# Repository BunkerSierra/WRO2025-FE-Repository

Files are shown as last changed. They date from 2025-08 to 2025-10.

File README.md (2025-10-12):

# Team Bunker Sierra – WRO Future Engineers 2025

We are a team from Baja California, México, composed of two members: Diego Alejandro Salas Díaz and Jacobo Arteaga Castañeda from Bunker Robotics. Both team members have experience in other competitions, specifically the Robomission category, totaling 8 years of combined experience.

This is our first year in the Future Engineers category. We began our preparation at the start of the year (January 2025), and over time, our robot has gone through several iterations. In fact, our current robot looks significantly different from the version used in the regional stage.

The following photo shows the 3 team members (from left to right):

Jacobo Arteaga Castañeda - Diego Alejandro Salas Díaz - Andrea Perez Bueno (Coach)

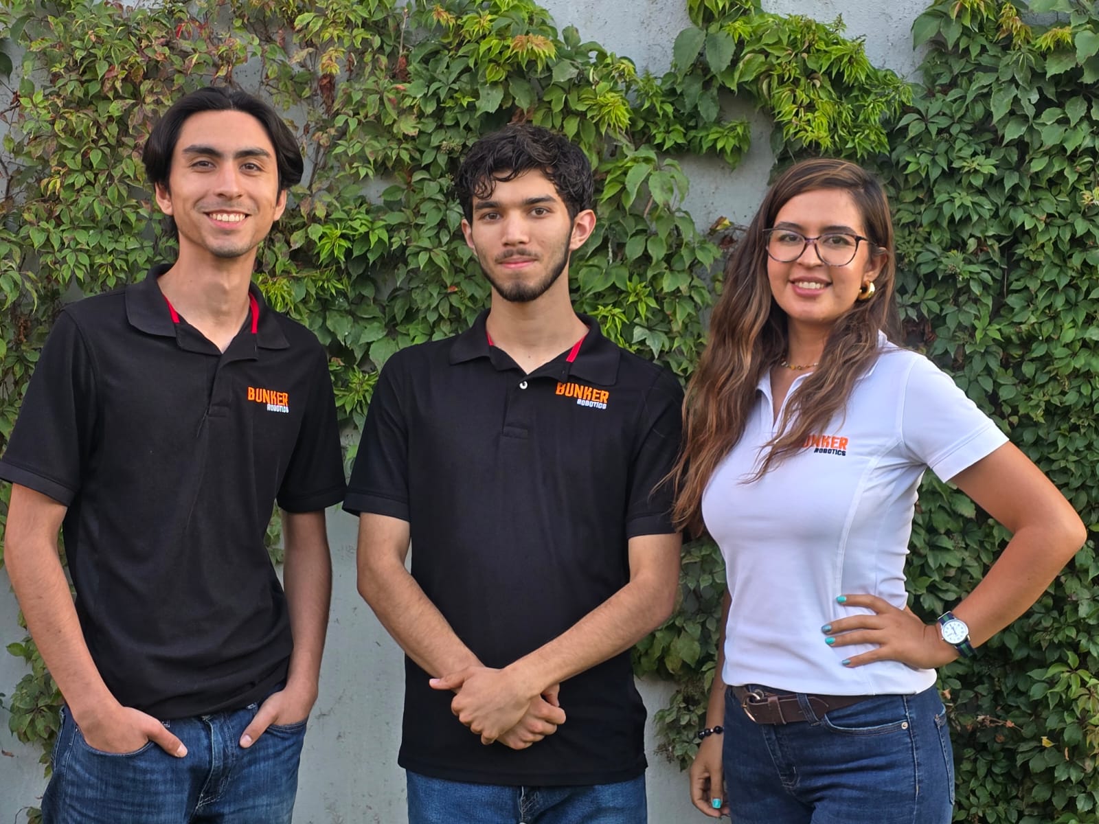
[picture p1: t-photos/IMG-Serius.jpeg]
IMG-Serius


In this document, we will detail our robot's components, their functions, and how they work together. We will also explain some of the key changes we have made to the robot, supported by visual evidence.

Please note: All requested supplementary information will be available in its corresponding folder within the repository.

## Robot Specifications:

**Vehicle photos rev.14 (Mexico National Final):**
| View | Photo |
|---|---|
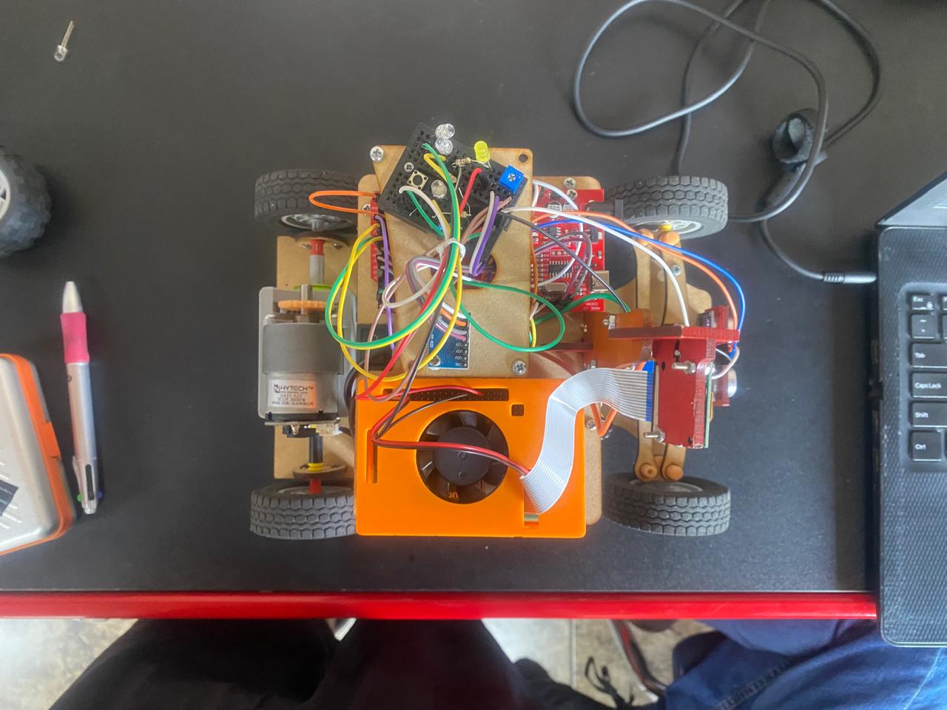
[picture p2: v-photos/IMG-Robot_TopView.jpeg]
IMG-Robot_TopView
| Top View |  |
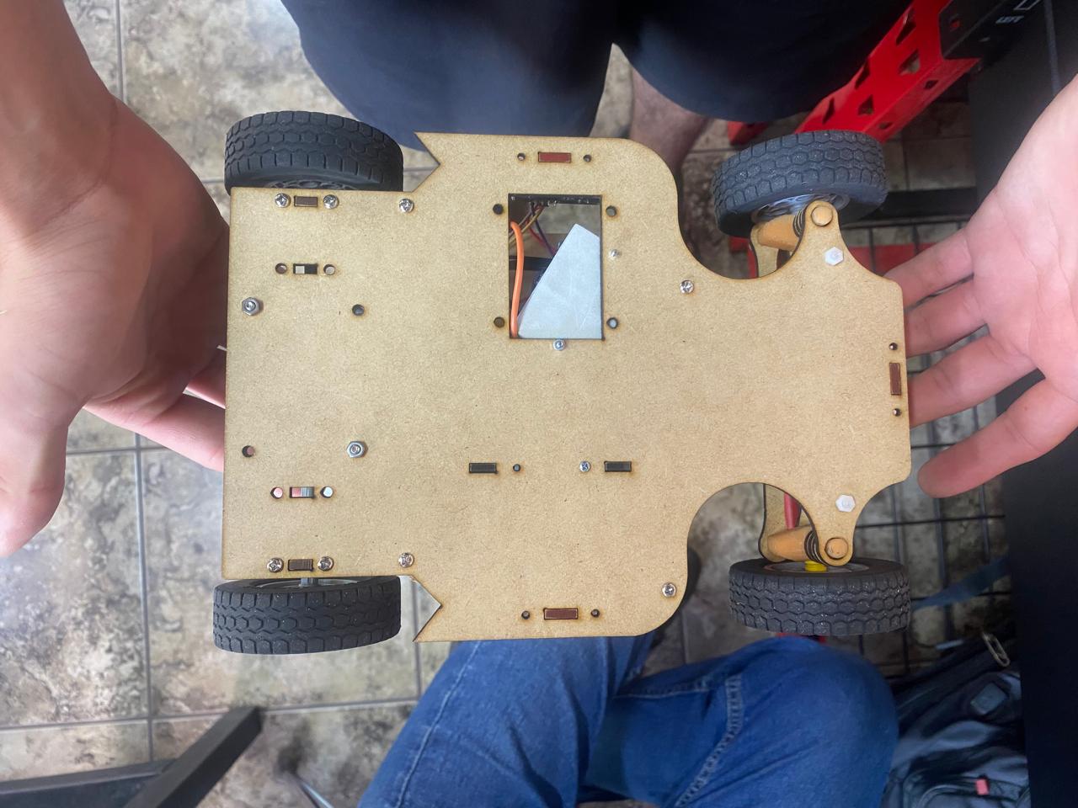
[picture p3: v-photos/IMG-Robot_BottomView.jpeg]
IMG-Robot_BottomView
| Bottom View |  |
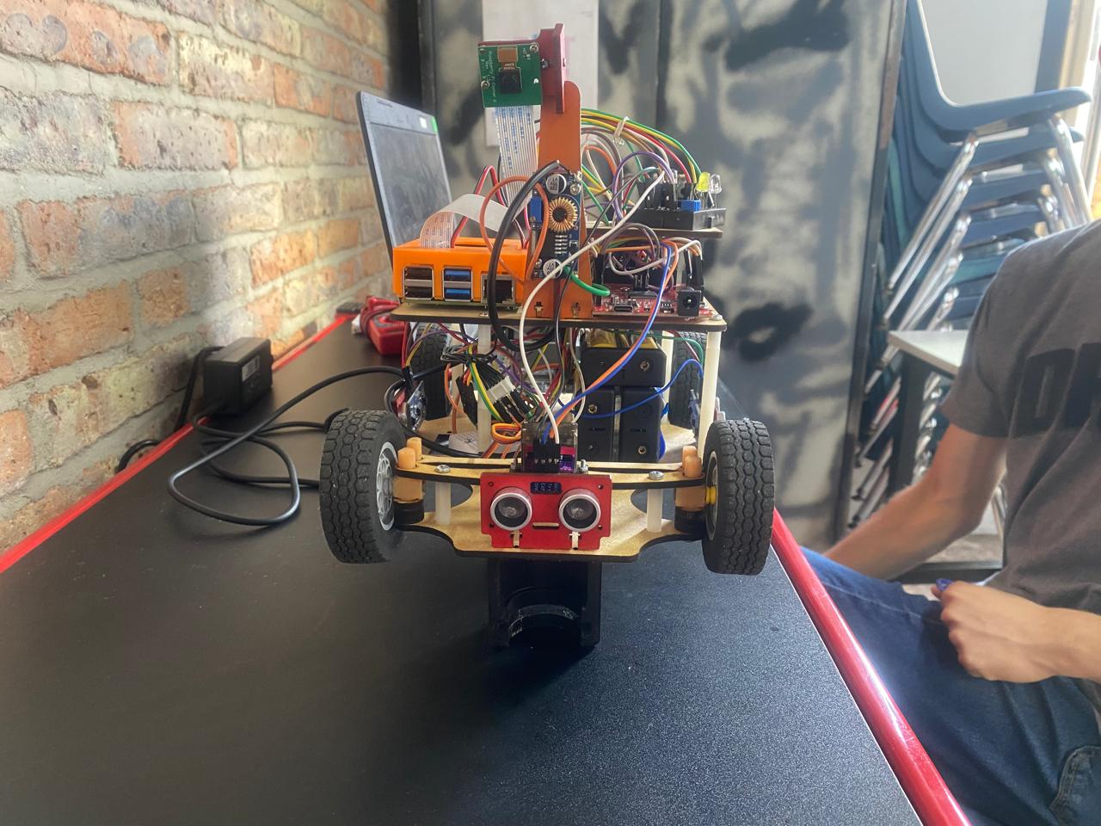
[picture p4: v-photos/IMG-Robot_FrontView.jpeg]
IMG-Robot_FrontView
| Front View |  |
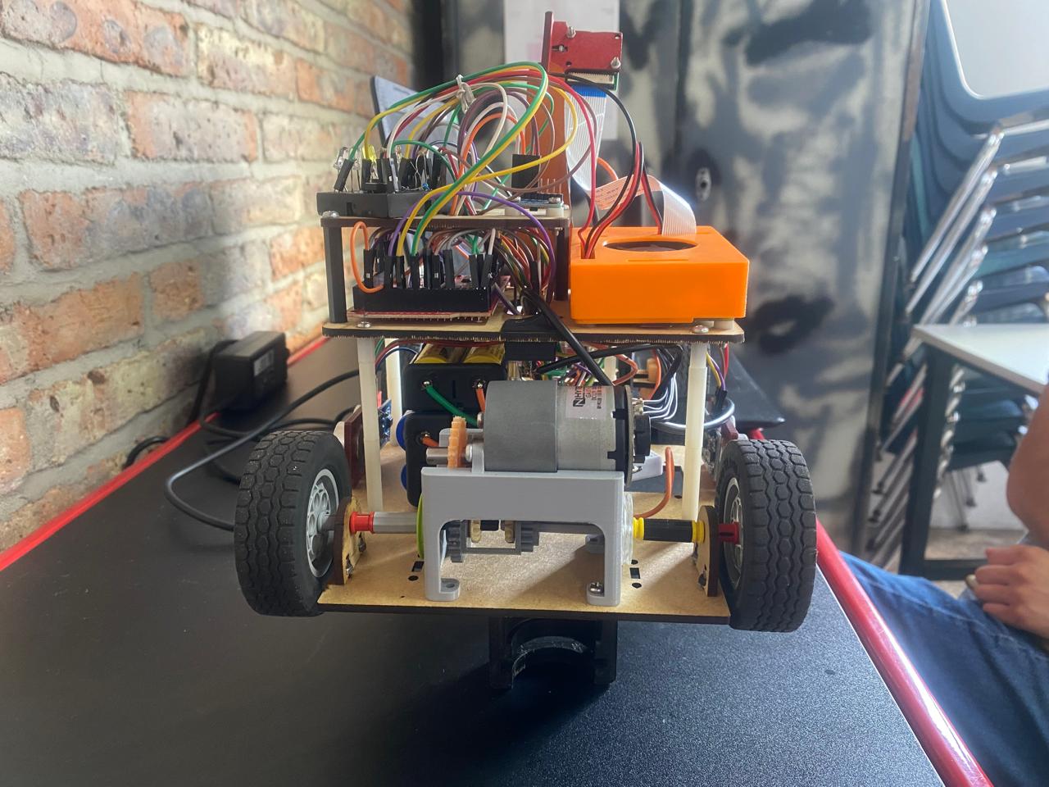
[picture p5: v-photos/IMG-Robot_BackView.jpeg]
IMG-Robot_BackView
| Back View |  |
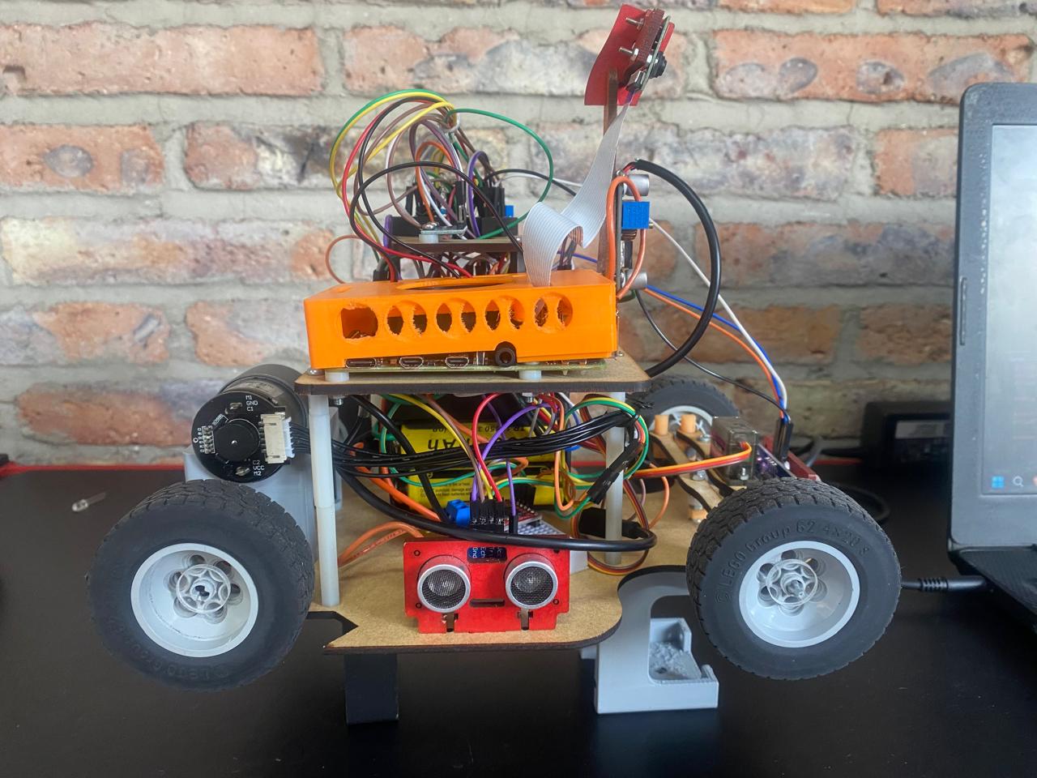
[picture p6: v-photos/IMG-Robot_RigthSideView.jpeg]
IMG-Robot_RigthSideView
| Right View |  |
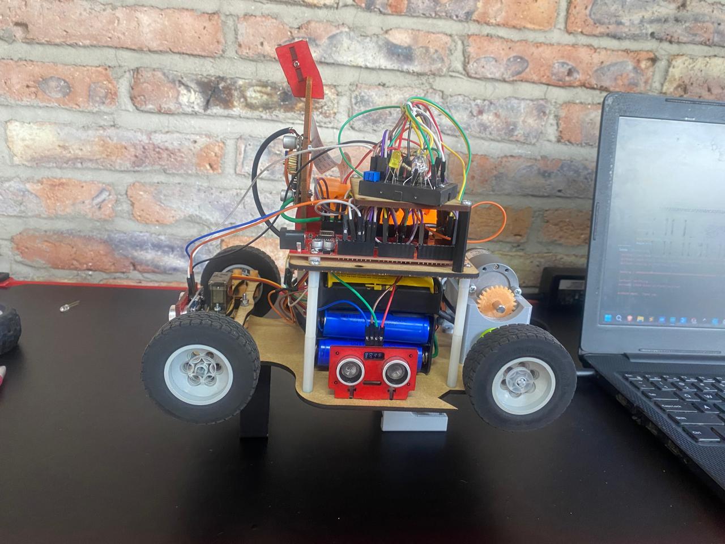
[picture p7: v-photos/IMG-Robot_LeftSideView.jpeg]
IMG-Robot_LeftSideView.
| Left View |  |

**Vehicle photos rev.15 (New rev. for OC Panama):**
| View | Photo |
|---|---|
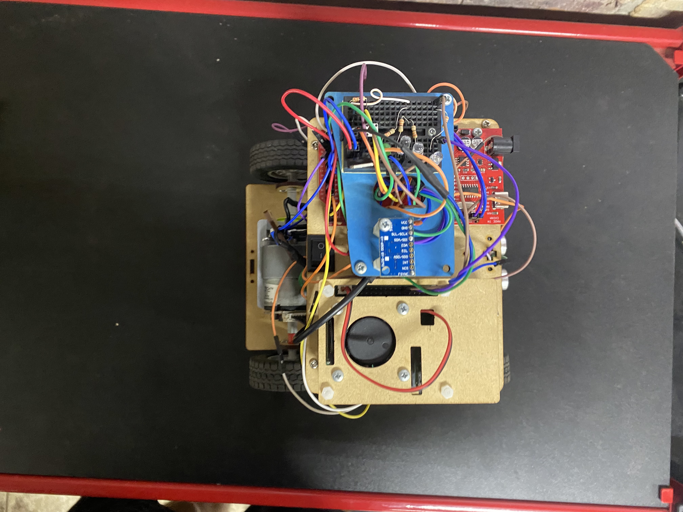
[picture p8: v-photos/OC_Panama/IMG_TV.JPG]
IMG_TV
| Top View |  |
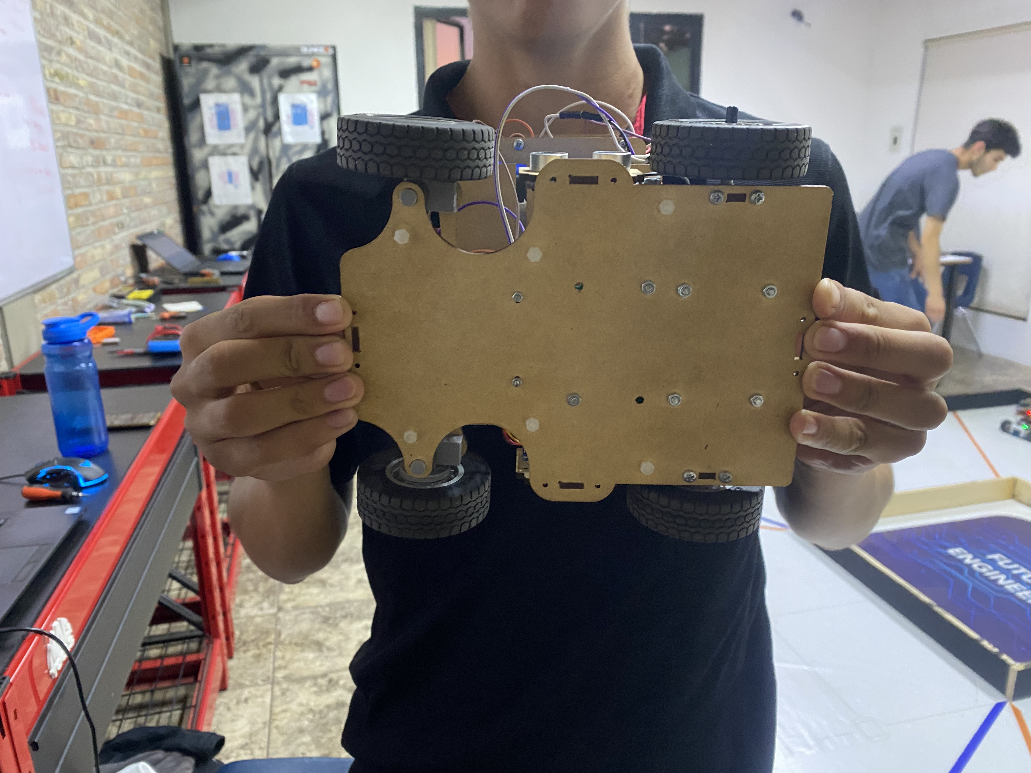
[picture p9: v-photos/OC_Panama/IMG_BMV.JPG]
IMG_BMV
| Bottom View |  |
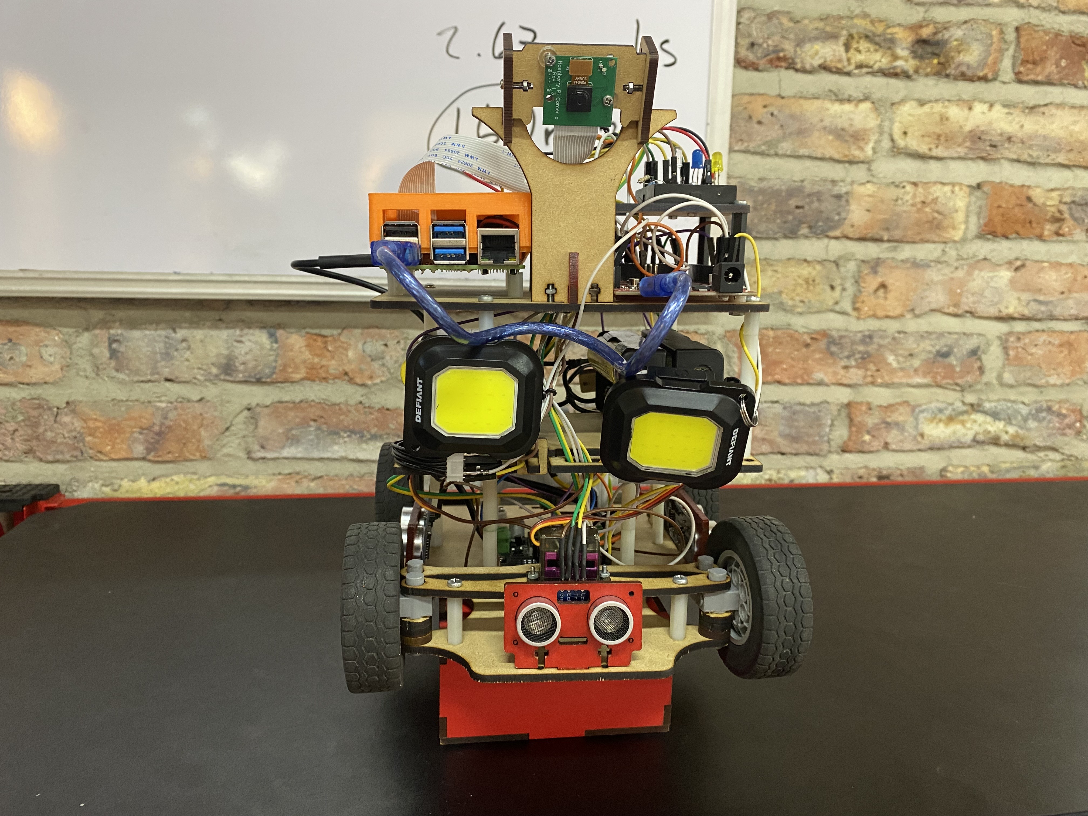
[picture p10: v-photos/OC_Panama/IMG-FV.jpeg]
IMG_FV
| Front View |  |
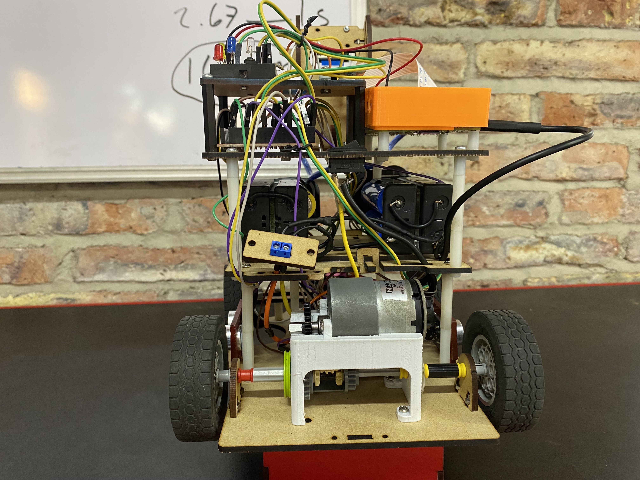
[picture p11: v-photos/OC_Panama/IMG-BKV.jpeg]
IMG_BKV
| Back View |  |
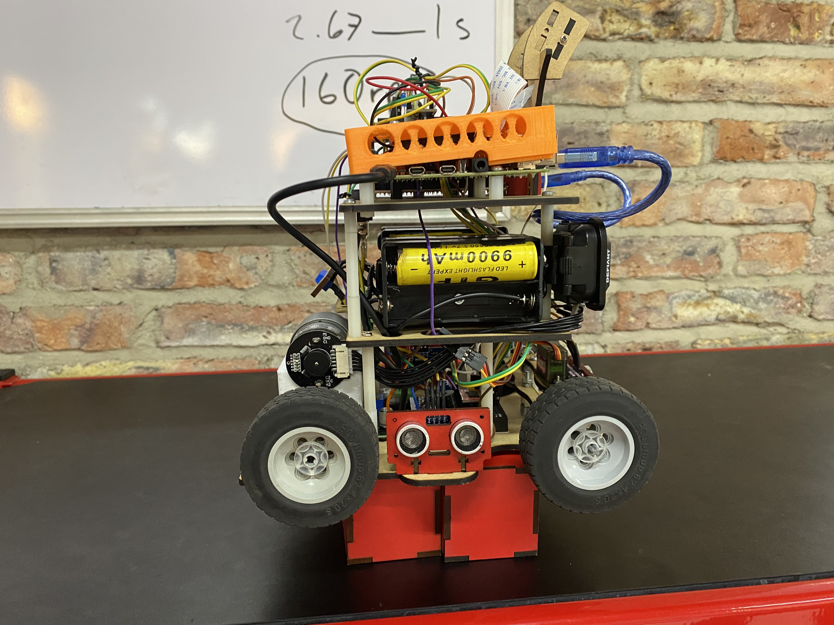
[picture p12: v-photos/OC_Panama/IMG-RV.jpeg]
IMG_RV
| Right View |  |
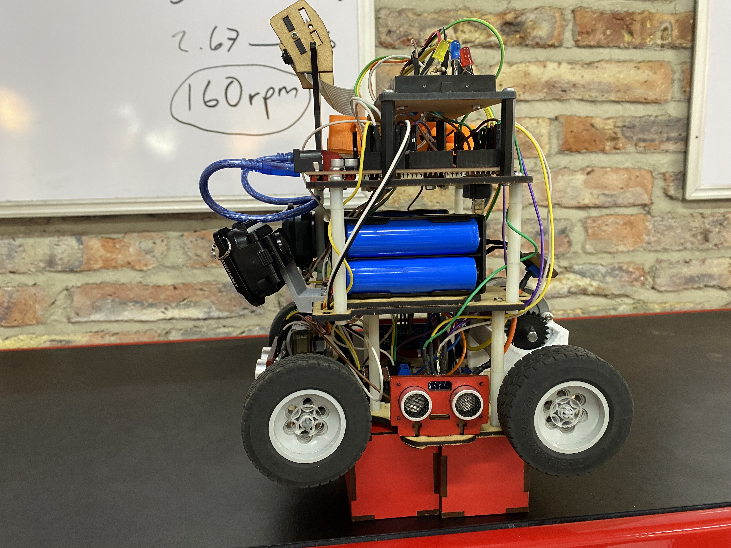
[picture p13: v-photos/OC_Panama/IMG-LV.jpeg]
IMG_LV
| Left View |  |

- **Weight (Maximum Load):** 1166 grams.
- **Width:** 1.5cm | **Length** 19.5cm | **Heigth:** 23.9cm

**Robot Bill of Materials (BOM)**

| Component | Power Requirements | Image | Price |
|---|---|---|---|
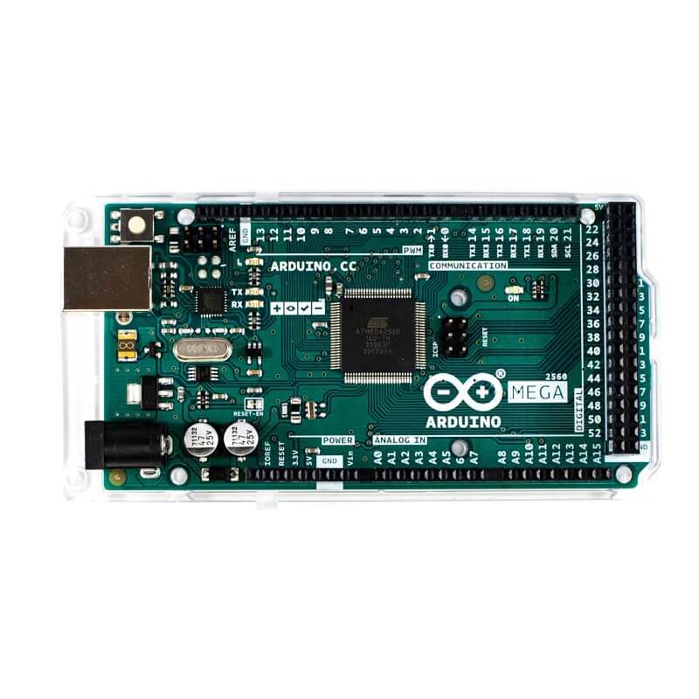
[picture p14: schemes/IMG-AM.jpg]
IMG-AM
| Arduino Mega 2560 | 0.25-0.5W |  | ≈ 24.46 Dlls |
| Raspberry Pi 4 Model B (1GB RAM) | 3.06-6.12W | IMG-RBPi4 | ≈ 46.90 Dlls |
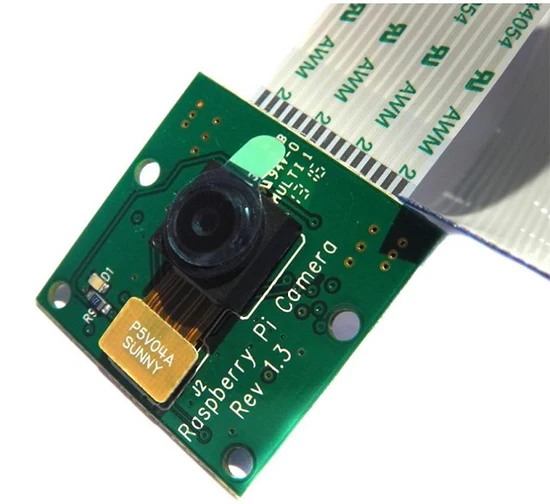
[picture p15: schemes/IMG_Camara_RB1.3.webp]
IMG_Camara_RB1.3
| Raspberry Pi Camera Rev 1.3 | 0.83W |  | ≈ 25 Dlls |
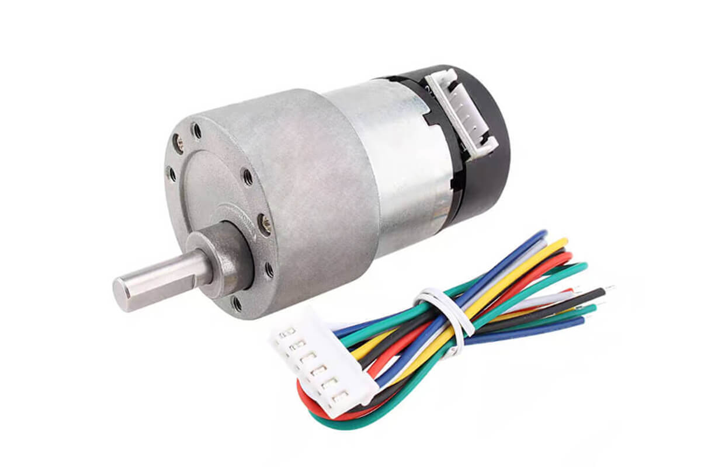
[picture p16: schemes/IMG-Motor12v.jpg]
IMG-Motor12v
| DC Motor with Encoder: GA37-520 300RPM | 5.55-16.65W |  | ≈ 22.12 Dlls |
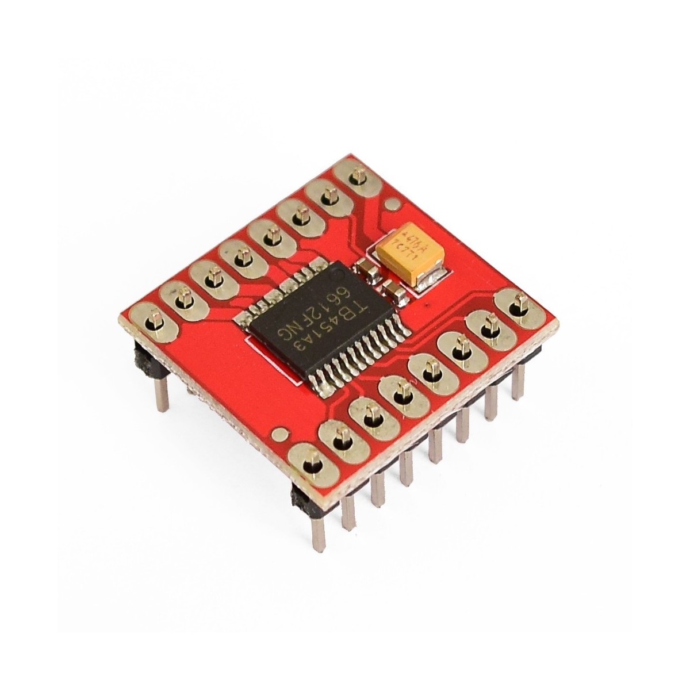
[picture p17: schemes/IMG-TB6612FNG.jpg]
IMG-TB6612FNG
| H-Bridge TB6612FNG | 0.025W |  | ≈ 4.35 Dlls |
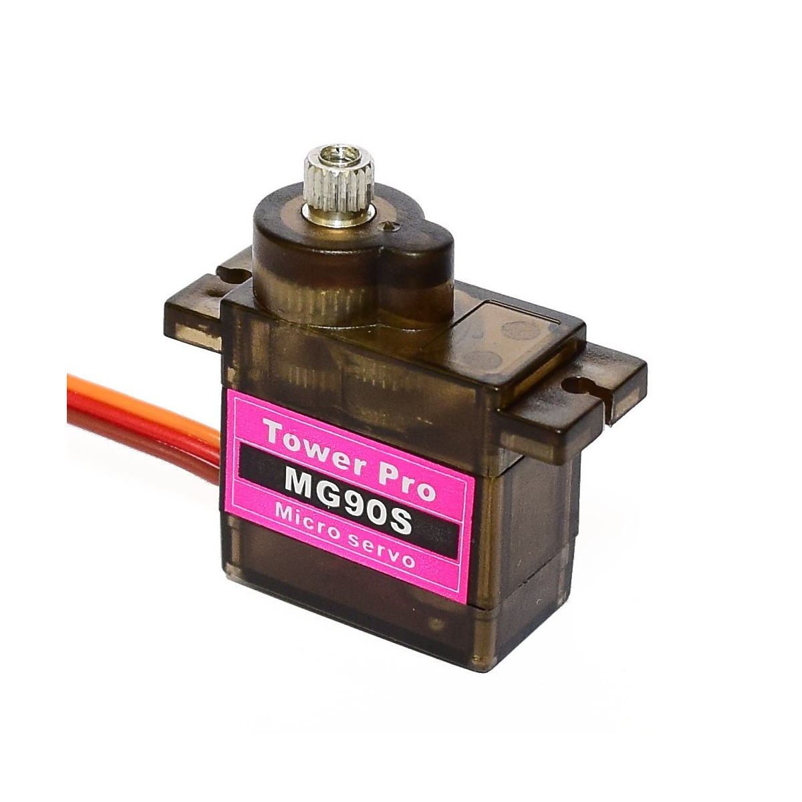
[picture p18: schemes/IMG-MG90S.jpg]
IMG-MG90S
| Servo Motor: MG90S | 0.5-2.5W |  | ≈ 4.08 Dlls |
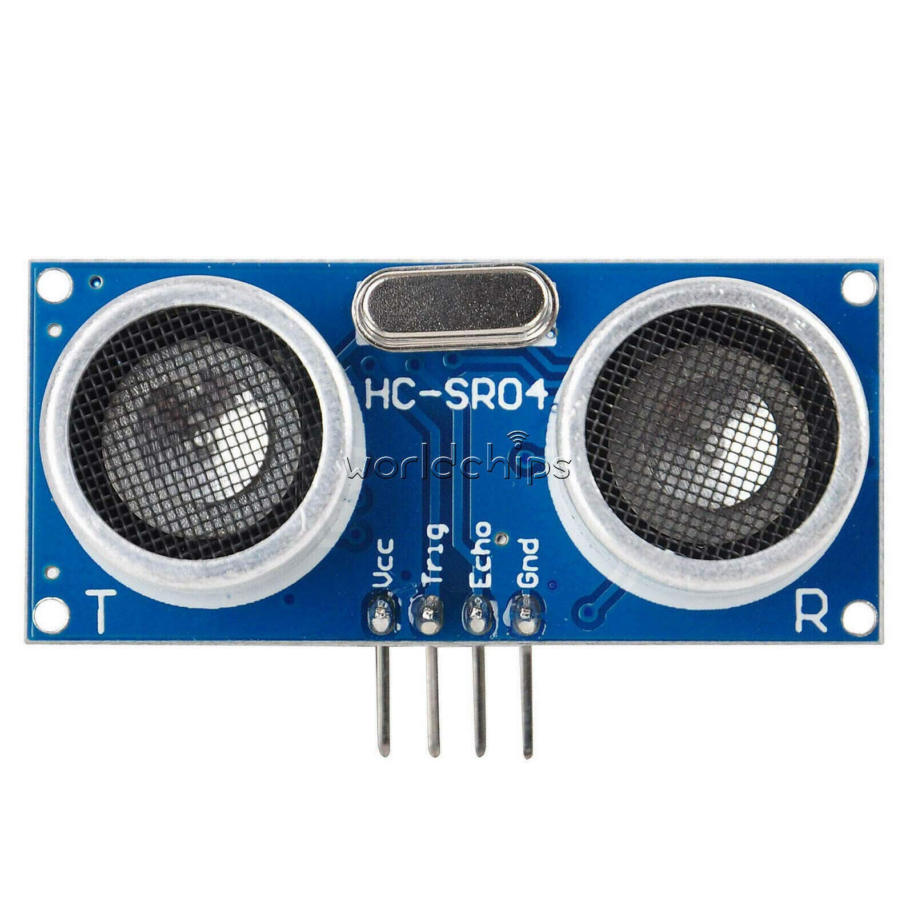
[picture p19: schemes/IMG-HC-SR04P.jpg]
IMG-HC-SR04P
| Ultrasonic Sensors: HC-SR04P x3 | 0.225W |  | ≈ 2.72 Dlls **(one unit)** |
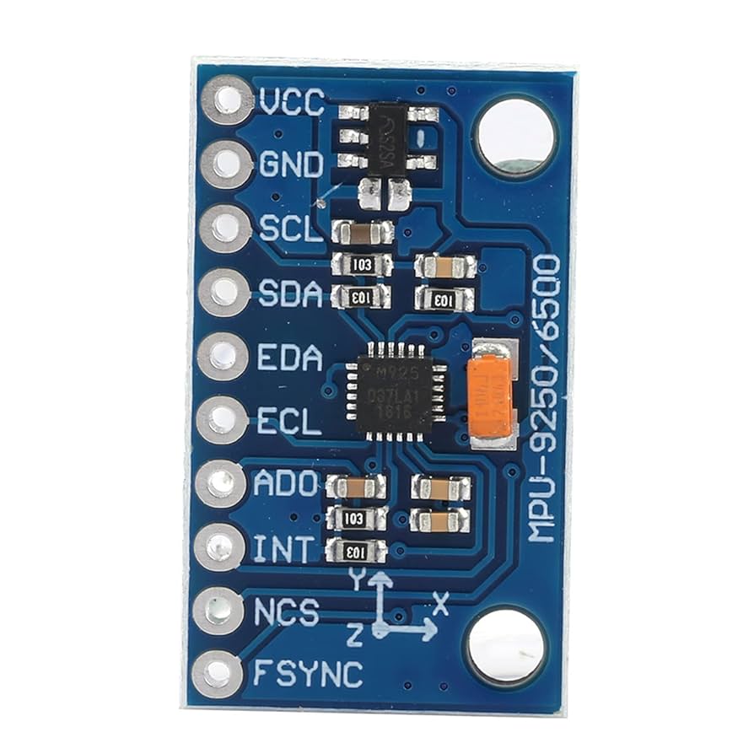
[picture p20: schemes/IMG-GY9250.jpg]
IMG-GY9250
| Accelerometer/Gyroscope: GY-9250 | 0.033W |  | ≈ 9.24 Dlls |
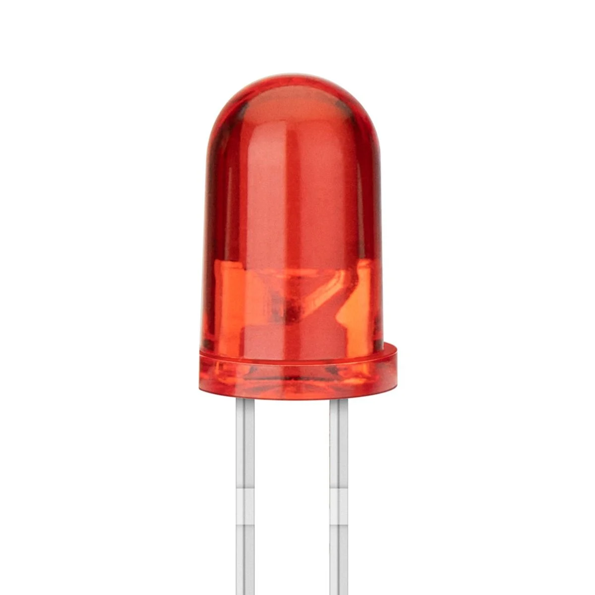
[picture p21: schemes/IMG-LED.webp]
IMG-LED
| LEDs x4 | 0.264W |  | ≈ 0.11 Dlls **(one unit)** |
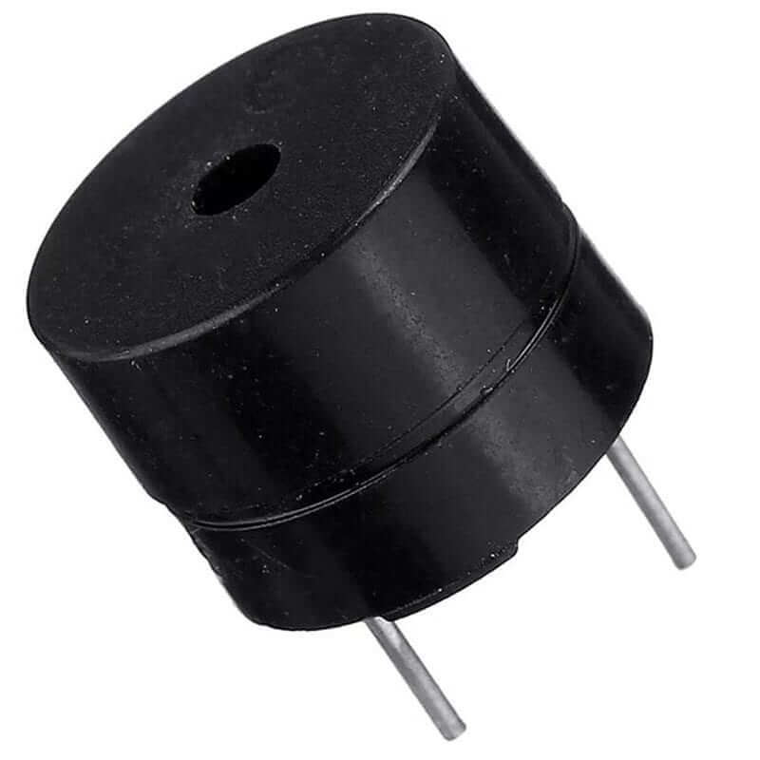
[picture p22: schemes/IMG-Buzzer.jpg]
| Passive Buzzer |  |  | ≈ 0.27 Dlls |
| **Total** | --- | --- | **≈ 145.02 Dlls** |

*Electrical Parts:*

- Arduino Mega 2560

- Raspberry Pi 4 Model B (1GB RAM)

- Raspberry Pi Camera Rev 1.3

- Motor Driver: IMS-2 WINGXINE

  - **Update 20/08/2025:** H-Bridge TB6612FNG

- Voltage Regulator: LM2596 Step-Down Module

- DC Motor with Encoder: GA37-520 300RPM

- Servo Motor: MG90S

- 3x Ultrasonic Sensors: HC-SR04P

- Accelerometer/Gyroscope: MPU-6050

  - **Update 12/09/2025:** Accelerometer/Gyroscope: GY-9250

- 4x LEDs

- Batteries: 6x 3.7v 18650 9900mAh

  - **Update 14/09/2025:** 8x 3.7v 18650 9900mAh

  - **Update 25/09/2025:** 3x 3.7v 18650 3000mAh
    
  - **Update 02/10/2025:** 6x 3.7v 18650 3000mAh

- Battery Holders: 3x 18650 Holders

  - **Update 14/09/2025:** 4x 18650 Holders

  - **Update 25/09/2025:** 2x 18650 Holders
    
  - **Update 02/10/2025:** 4x 18650 Holders

- 1x Passive Buzzer

- 2x Mini Protoboards

*Mechanical Parts:*

- MDF Chassis x3

- MDF Linkage Steering System

- 4x Lego Wheels (62.4mm x 20mm)

- 3D-Printed Motor Mount

- Raspberry Pi Camera Rev 1.3 Mounts

- 3x Ultrasonic Sensor Mounts

- Lego Differential Gear

- 3D-Printed Spur Gear (24-tooth)

- Lego Technic Parts

**Update 25/09/2025**

***Update for the Panama Open Championship***

We have implemented several changes to the robot's design, specifically focusing on reducing its footprint. In other words, we have reduced the robot's width and length while taking full advantage of the established height limit (30 cm). We have redistributed the components accordingly to optimize the use of space.

Here is the list of the STL desings of all the parts of the robot chassis that where changed:

- [S25 Chassis Rev15B](/models/Open_Championship_Panama/S25_Chasis_Rev15B.STL).
- [BS Batteries Rev3.STL](/models/Open_Championship_Panama/BS_Baterias_Rev3.STL).
- [C3 Batteries Rev3.STL](/models/Open_Championship_Panama/C3_Baterias_Rev3.STL).
- [S25 Level 3 Rev3.STL](/models/Open_Championship_Panama/S25_3er_Piso_Rev3.STL).

We have also significantly reduced the robot's turning circumference. Previously, when the robot executed a full turn, the diameter of the circle it traced was 62 cm. This was quite large and allowed the robot to collide easily with the field's barriers and obstacles (in both challenges). By reducing the robot's overall size, the turning circle diameter is now 30 cm. We managed to cut it in half, giving the robot a greater margin of error to avoid collisions with various objects on the field. 

Another major change was made to the robot's power system. To be frank, our previous design was poorly planned. For the Open Championship, we opted to use **two packs in parallel of three 3.7V 30000mAh batteries connected in series(3S2P)**. 

Finally, we added two lamps to the robot to improve our camera's optics. By generating our own light source, detecting obstacles becomes a simpler task, as it no longer depends on the varying light conditions and parameters of the different environments where the robot operates. 

Here is the list of the STL desings of the camera parts that where changed:

- [Light L Mount](/models/Open_Championship_Panama/Soporte_L_Rev1.STL).
- [Camera Mount_Rev3](/models/Open_Championship_Panama/Soporte_Camara_Rev3.STL).

This is the brand and especifc model of the lamps tha wew used: **Defiant 226 129**

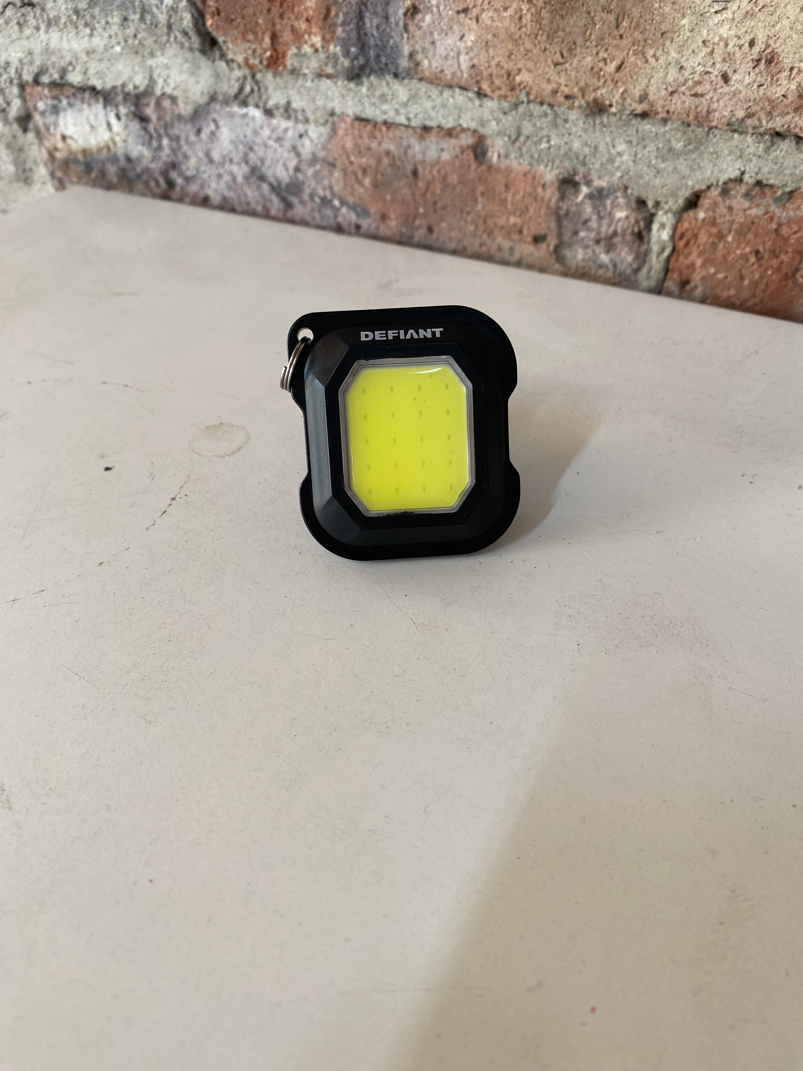
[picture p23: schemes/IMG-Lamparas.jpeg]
IMG-Lamparas


Mechanical Parts
===

*You are about to see all the information contained in our [models](/models/README.md). folder. If you wish to only view the information from this specific section, you can access it directly via the hyperlink (with the exception of the updates for the Panama Open Championship).*

One key point we would like to emphasize is that the majority of our mechanical parts were manufactured using laser cutting. Another small section of parts, primarily for the steering system, were 3D-printed.

## Vehicle Chasis
The vehicle consists of a chassis and two additional levels (floors), each housing different robot components:

- **Chassis:** Robot Motion Management
  - Steering system, DC drive motor, Motor driver, and a Mini Protoboard.
  - [Chassis View](/models/S25_Chasis_Rev12.STL).
- **Level 1:** Robot Controllers
  - Arduino Mega, Raspberry Pi y RaspBerry pi Camara rev 1.3
  - [Level 1 View](/models/S25_BS_Rev6.STL).
- **Level 2:** Electrical Components
  - Mini Protoboard with HMI and Gyro sensor.
  - [Level 2 View](/models/S25_Piso3_Rev1.STL).
 
As you may notice, the filenames for all models include their revision number. For example, the chassis is on its 12th revision. This reflects every change we have needed to make throughout the season. It is the part that has undergone the most changes.

As mentioned in other sections of the repository, our robot looked very different during the regional stage compared to its current form for the national stage. This is the main reason why this particular part has been modified so extensively. It was from **Rev8** onwards that it began to take on its current appearance.

**Update 14/09/2025**

**1. Chassis and Power System Modification**

**Motivation:** During performance testing for the obstacle challenge, we observed excessive energy consumption from the Raspberry Pi module. This was causing a rapid voltage drop in the batteries (~0.08V per complete run), which compromised the robot's operational autonomy to successfully complete multiple attempts or competition rounds.

**Implemented Solution:** To resolve this energy bottleneck, we expanded the power system by integrating a fourth battery holder, connected in parallel with the existing ones. This configuration:

**Increases the total capacity (Ah)** of the battery bank.

**Maintains the nominal operating voltage** for all components.

**Provides greater autonomy** by distributing the current demand across more power sources.

**Additional Changes:** As part of the chassis reconfiguration, we re-optimized the placement of the voltage regulator and the protoboard to improve accessibility, aesthetics, and cable management.

- [S25_Chasis_Rev14](/models/S25_Chasis_Rev14.STL).

To keep the battery holders securely in place, we designed another component (there are two of these in the robot) capable of holding two battery holders simultaneously. You can view the part here:

- [SB_DrakoR_Rev2](/models/SB_DrakoR_Rev2.STL).

## Mobility Management
**Motor Mount**

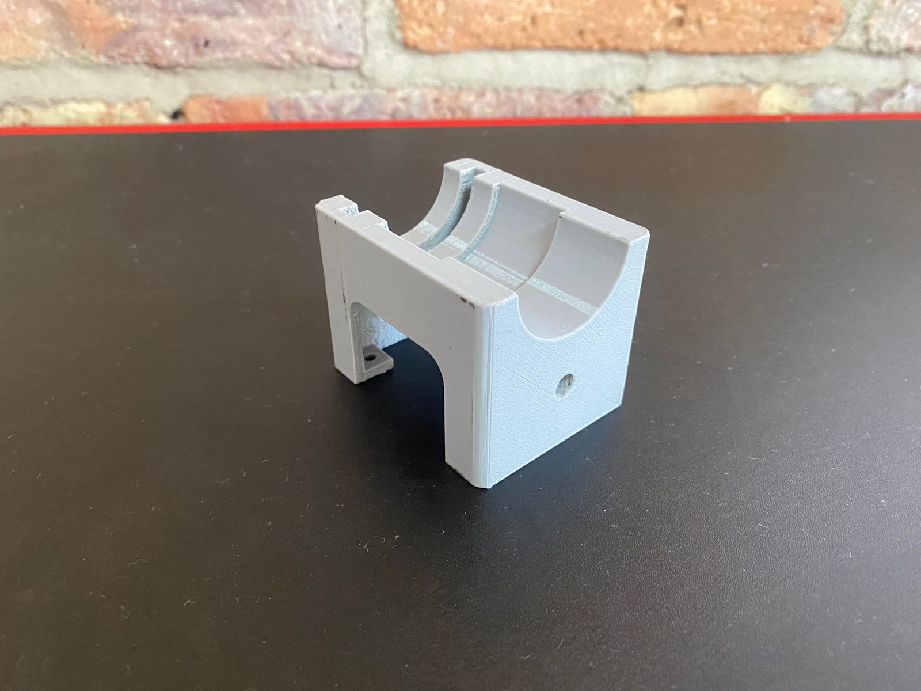
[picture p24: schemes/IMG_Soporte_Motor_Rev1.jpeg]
IMG_Soporte_Motor_Rev1


*This is what the first version looked like. It allowed for basic testing, but the motor was not secured to the mount, which caused disturbances and instability.*

-[Soporte para motor Rev3](/models/S25_Soporte_Motor_y_Transmision_Rev3.STL) 

*In the current revision, the motor is firmly secured to the mount, eliminating disturbances caused by movement.* We had a similar case with the gear that connects to the motor.

**Motor Axle Support**

The output shaft of our motor couples to LEGO axles that are connected directly to the wheels. During initial testing, we noticed that these axles were bending. This created an undesired additional force on the motor's Z-axis and caused inconsistent performance in each test run.

As a solution, we designed and implemented a custom support for these axles. Once installed, the axles remain perfectly aligned at a 180° angle, eliminating bending and ensuring uniform and predictable behavior.
- [Motor Axle support](/models/S25_Soporte_Eje_Motor_Rev1.STL).

**24-Tooth Spur Gear**

Initially, we used a standard 24-tooth LEGO Spur gear, drilling out its center to fit the motor's main shaft. This allowed us to validate the behavior of the differential system.

However, this provisional solution had two critical problems: the hole was quickly deformed by wear and tear, and it generated considerable backlash. To resolve this, we designed our own gear, maintaining the standard LEGO dimensions but with the exact inner diameter for our shaft. This ensured a perfect fit and eliminated the backlash.

- **Old Gear:**

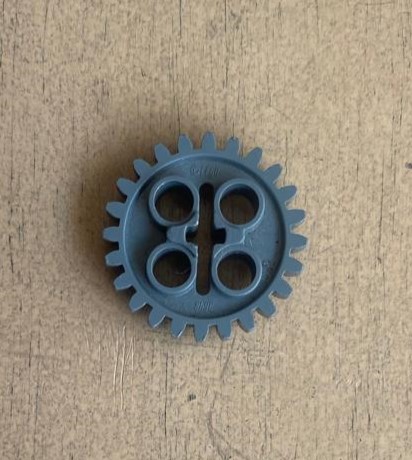
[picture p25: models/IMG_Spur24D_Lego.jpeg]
IMG_Spur24D_Lego
  - 

- **Proposed Gear by the Team:**

  - [New Custom Gear](/models/S25_Spur_24D_Rev3.STL)

**Steering System** 

Our steering system operates through a **linkage mechanism** connected to the **steering knuckles**. At the center of one of these links, a custom-made component is directly attached to an **MG90S servo motor**, allowing us to position the steering mechanism precisely at the specific angles required by our navigation algorithm.

The links were manufactured from **MDF** due to its rigidity and low weight, while the knuckles and connectors were 3D-printed to achieve complex geometries and reduced weight.

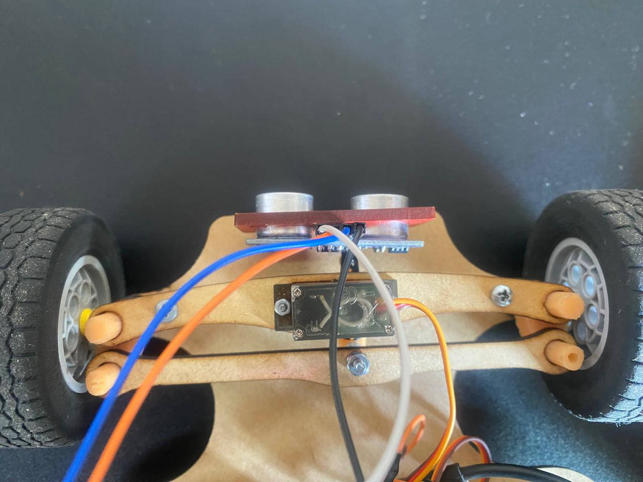
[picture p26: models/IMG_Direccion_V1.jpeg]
IMG_Direccion_V1

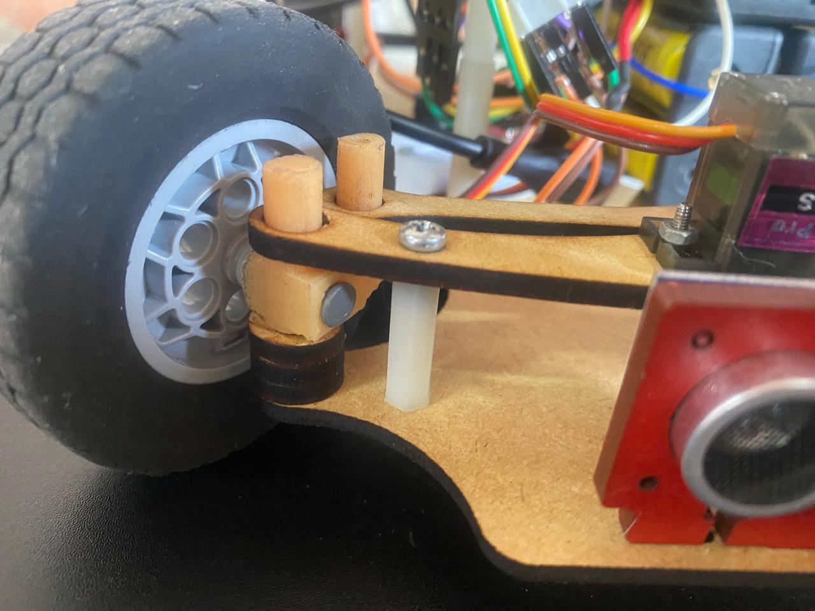
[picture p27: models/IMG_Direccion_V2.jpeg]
IMG_Direccion_V2


- **Steering System Components:**
  - [Servo to Beam 1 Connector](/models/S25_Conexion_Servo-enlace_Rev2.STL).
  - [Beam 1](/models/S25_Enlace_Direccion_Rev5.STL).
  - [Beam 2](/models/S25_Soporte_Servo_Rev4.STL).
  - [Spacers](/models/S25_Rondana_Direccion_Rev1.STL).
  - [Steering Knuckles](/models/S25_Mangueta_Rev1.STL).

The last component (steering knuckles) was printed in two versions: one with the original design and another mirrored version.

**Wheels**

We use **62.4mm** LEGO wheels due to our positive experience with them in previous Robomission competitions. We trust their excellent **grip** and the **low rolling resistance** they generate, which is crucial for the robot's energy efficiency and traction.

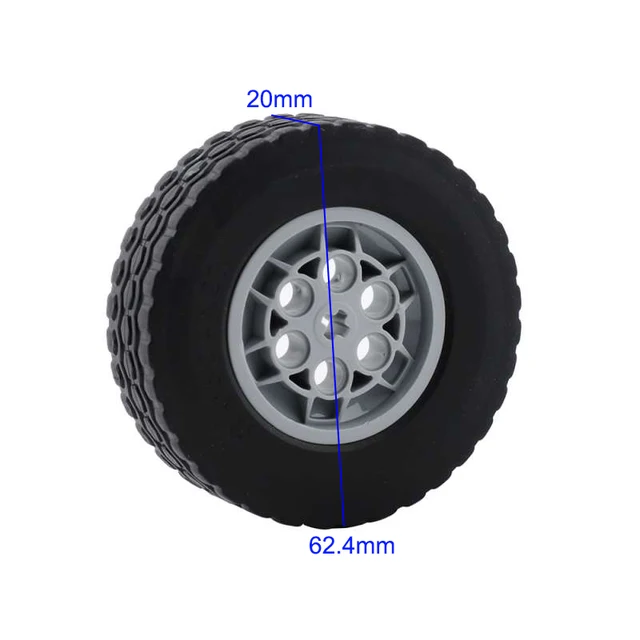
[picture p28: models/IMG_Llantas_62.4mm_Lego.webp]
IMG_Llantas_62.4mm_Lego


## Obstacle Management

**Camera Mount**

The vision system is composed of several custom parts:

  - [Post Mount](/models/S25_Soporte_Poste_Camara_Rev1.STL).
  - [Post](/models/S25_Poste_Camara_Rev1.STL).
  - [Camera Mount](/models/S25_Soporte_Camara_Rev1.STL).
  - [70-Degree Joint](/models/S25_Union_70_grados_Camara_Rev1.STL).

The **height** and **tilt angle** of the camera are critical for our algorithm. The configuration must allow the robot to detect obstacles within a specific quadrant of the track.

- A **90°** (vertical) tilt did not allow for early detection.

- An initial **45°** tilt pointed the camera too far down, detecting obstacles too late.

- After a process of **trial and error**, we determined that a **70°** angle was optimal for our use case, as it provides the necessary field of view for timely and reliable detection.

**Update 07/09/2025**

We changed the camera mount angle to 63° and raised the mount height by 1/8 inch. Previously, with the mentioned specifications, the robot had a very low margin of error for positioning itself in front of obstacles and failed when detecting the position and color of the obstacles.

**Camera Angle and Height Optimization**

To improve reliability in detecting obstacle position and color, we adjusted the configuration:

- **Tilt Angle:** Changed from **70°** to **63°**.
  
[S25_Union63_grados_Poste-Soporte_CamaraRev2](/models/S25_Union63_grados_Poste-Soporte_CamaraRev2.STL).

- **Mount Height:** Increased by **1/8 inch**.
  
[S25_Soporte_CamaraRev2.STL](/models/S25_Soporte_CamaraRev2.STL).

The previous configuration, while functional, provided a **very low margin of error** for the robot to position itself correctly in front of obstacles. These fine adjustments significantly increased the success rate of detection and positioning.

## General Vehicle Electrical Diagram: 

*You are about to see all the information contained in our [schemes](/schemes/README.md). folder. If you wish to only view the information from this specific section, you can access it directly via the hyperlink (with the exception of the updates for the Panama Open Championship).*

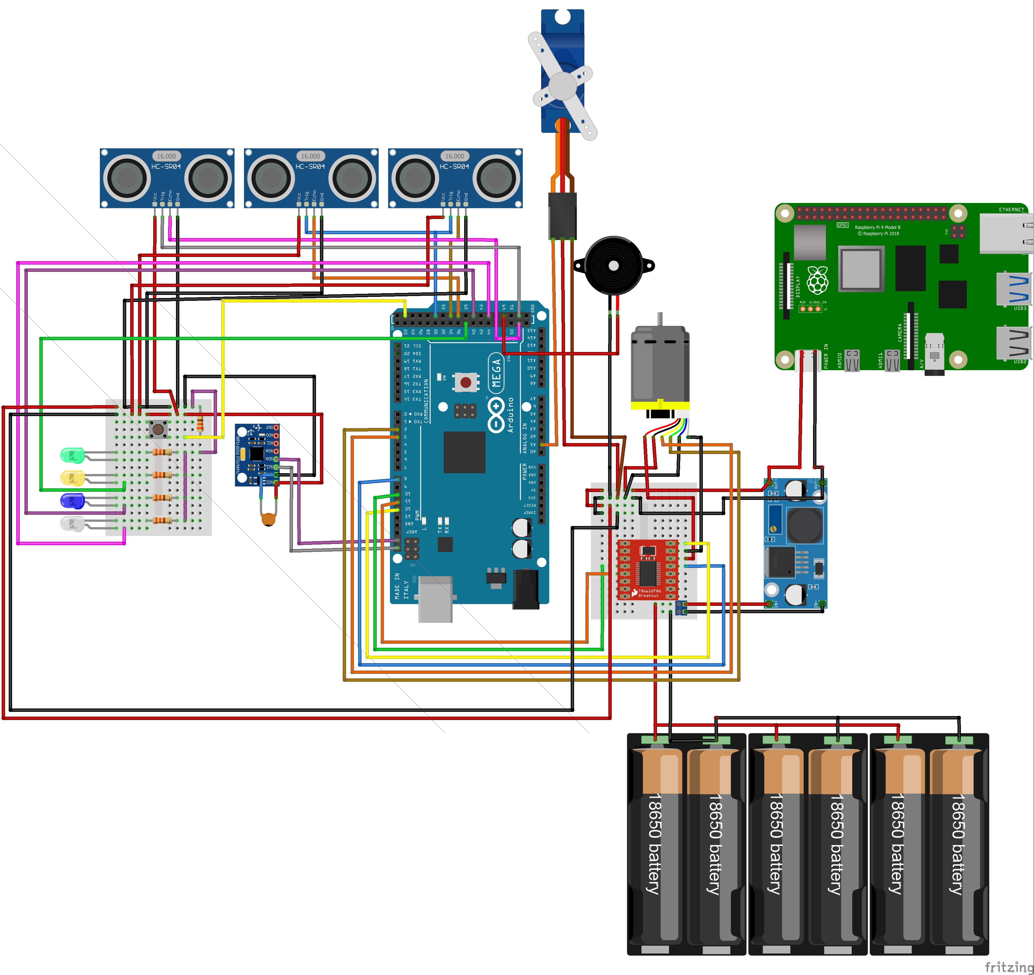
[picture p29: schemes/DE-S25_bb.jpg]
DE-S25_bb


***Specifications:*** The **Arduino MEGA** board is powered directly through the serial communication port of the **Raspberry Pi 4** computer. The Raspberry Pi, in turn, is powered by our **LM2596** voltage regulator, set to **5.1V** and **3A**. We adjusted the regulator to 5.1V because when set exactly to 5V, the Raspberry Pi would often experience power supply issues.

## Electrical Diagrams for Each Component and Sensor:

***Clarification:*** The following diagrams show the signal connections for each sensor and electrical component. **Only* the **Power System** and **Motor with Motor Driver** diagrams include the power supply connections, as these are essential for replicating the robot. The other diagrams omit these connections to provide flexibility for other teams, but they can be referenced in the **General Electrical Diagram** shown above.

- **Ultrasonic Sensors**
  
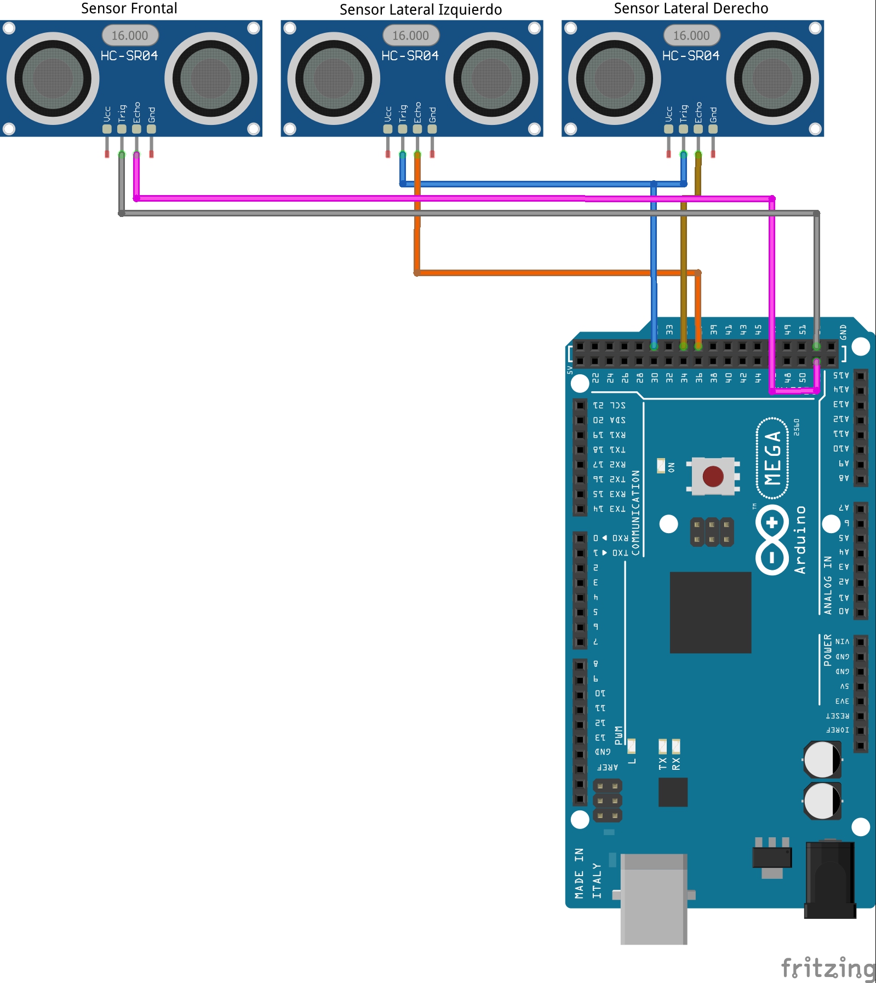
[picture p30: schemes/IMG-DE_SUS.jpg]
IMG-DE_SUS


- **Accelerometer/Gyroscope**
  
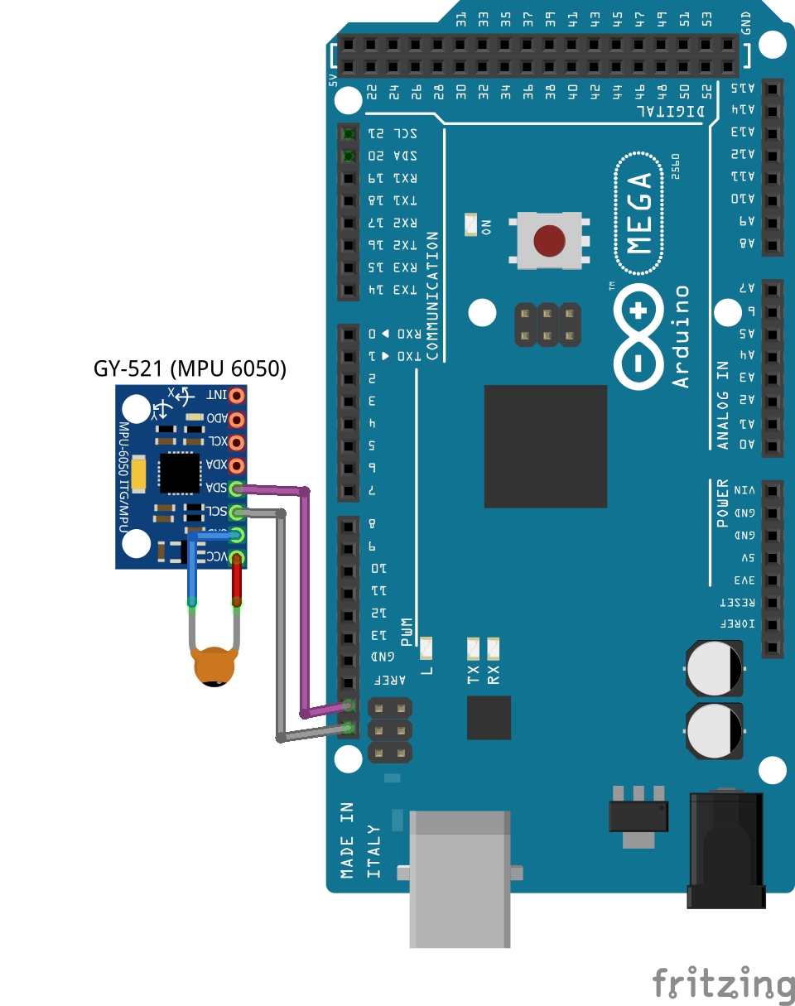
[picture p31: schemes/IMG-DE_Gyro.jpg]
IMG-DE_Gyro


- **Servo Motor**
  
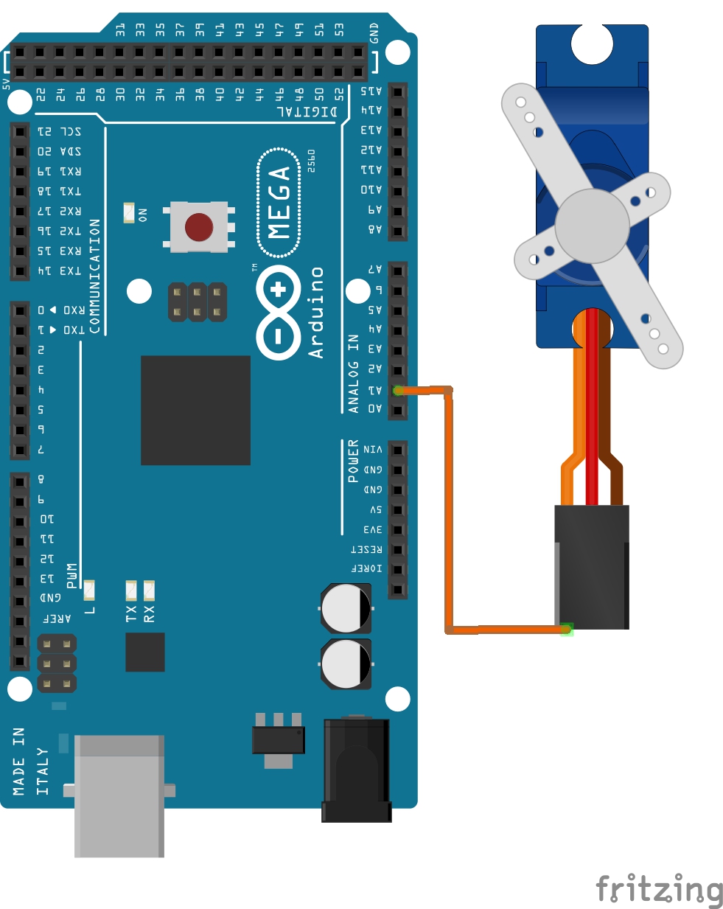
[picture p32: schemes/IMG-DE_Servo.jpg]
IMG-DE_Servo


- **Human Machine Interface**
  
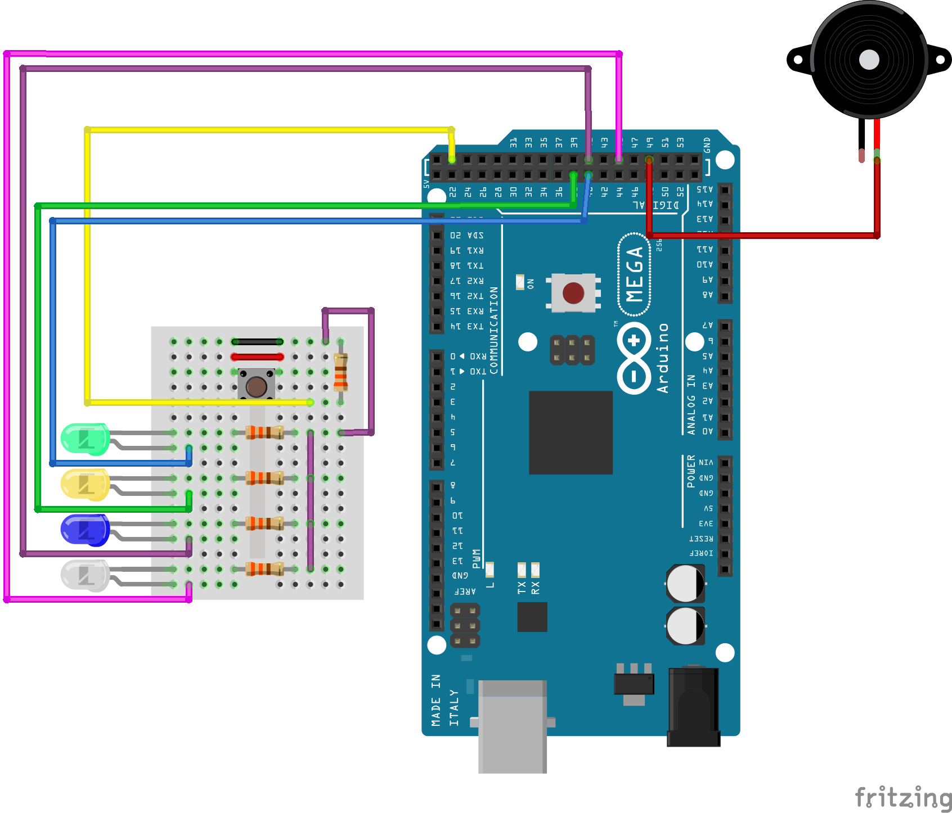
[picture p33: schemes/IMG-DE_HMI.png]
IMG-DE_HMI


- **Motor 12v - Motor Driver**
  
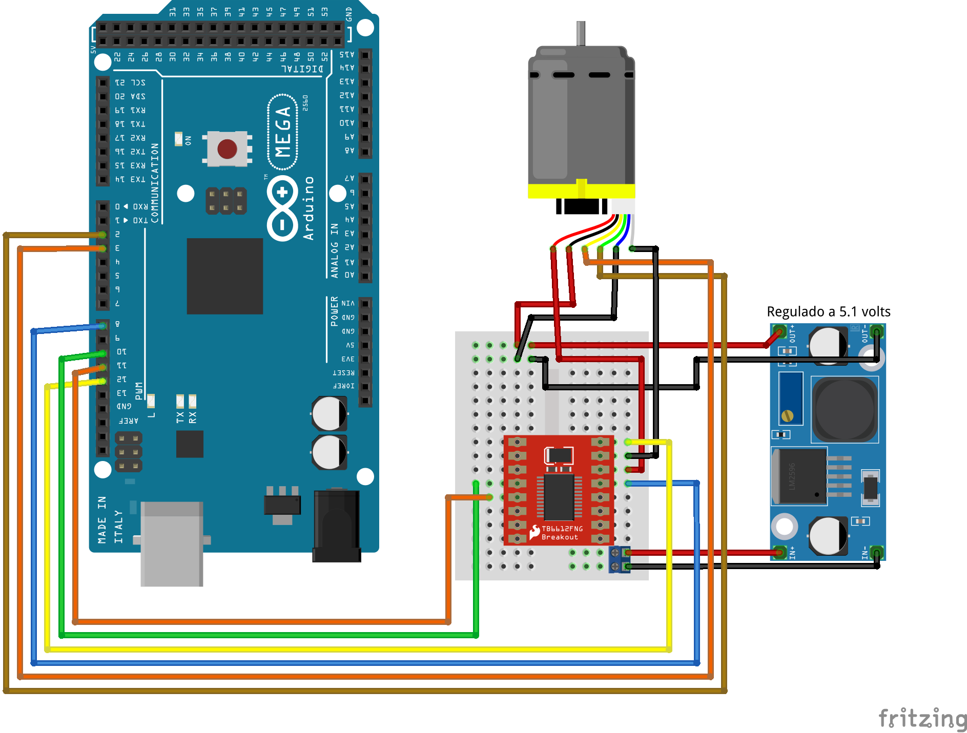
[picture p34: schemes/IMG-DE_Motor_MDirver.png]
IMG-DE_Motor_MDirver


- **Power Stage and Raspberry Pi 4**
  
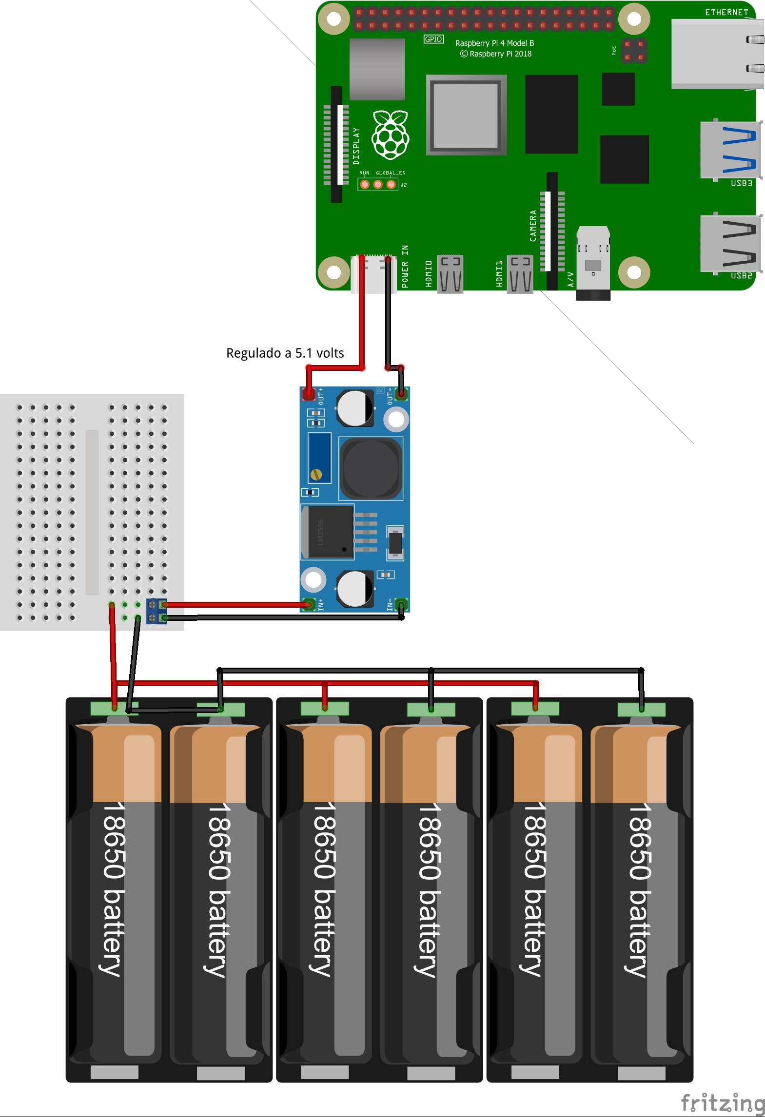
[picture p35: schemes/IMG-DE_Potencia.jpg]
IMG-DE_Potencia


  **Update 25/09/2025**
  ***Update for the Panama Open Championship***

  The following picture shows the new configuration of the robot's battery pack **(3S2P)** mentioned earlier in the repository:
  
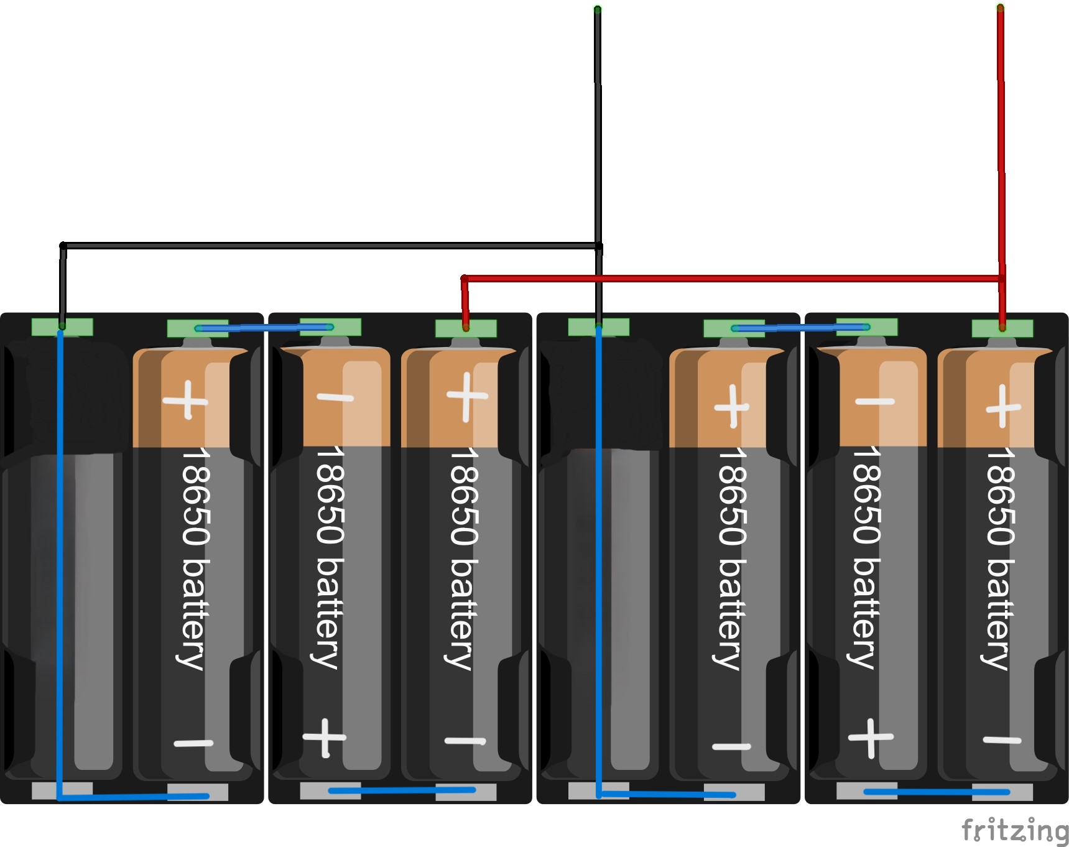
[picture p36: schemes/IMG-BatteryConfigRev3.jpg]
IMG-BatteryConfigRev3
  

Mobility Management
===
## 12V DC Motor with Encoder
We selected this motor primarily for its **integrated encoder**. This sensor allows us to track the robot's position, which provides multiple benefits for our solution: calculating rotation count, measuring distance traveled, assisting in parallel parking, and, in general, all variables related to positioning.

IMG-Motor12v

Initially, we used a motor from an RC toy that included a differential. We used that motor during the regional stage in Mexicali. We decided to change it because its speed was too inconsistent, and the lack of an encoder made it very difficult to maintain consistent movements. We understand that it's impossible for a robot to repeat a routine exactly, but that component made it even more challenging. Switching to a motor with an encoder and a LEGO differential gives us much greater control over these variables. To achieve this, we designed a mount to couple the motor to the LEGO differential, which went through 3 revisions.

## Movement 
To make the robot move in a straight line, we use a gyro sensor with a PD controller. This allows the robot to maintain its heading. As mentioned before, it's impossible to be perfect, but with this system the deviation is minimal, never exceeding 2° from the initial point (considering 0° as the origin).

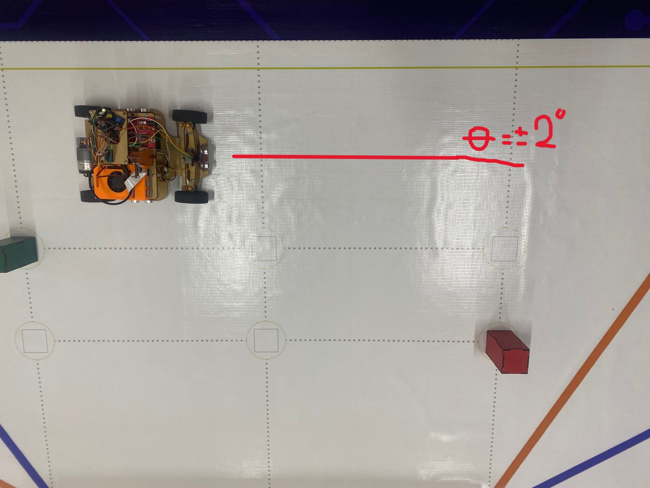
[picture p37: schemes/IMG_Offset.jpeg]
IMG_Offset


To calculate the robot's deviation without the gyro sensor's PD control, we conducted 10 tests where the robot advanced 3 meters. During these tests, we realized the robot had a very large deviation, with an average of 14° deviation ± a standard deviation of 18°.

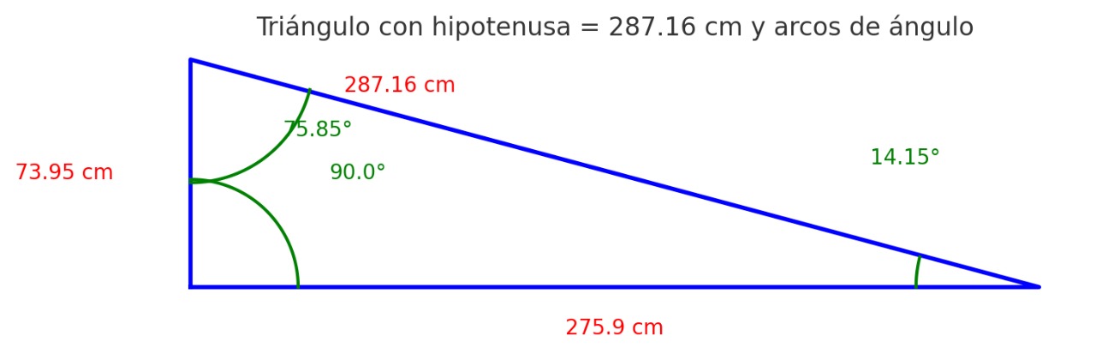
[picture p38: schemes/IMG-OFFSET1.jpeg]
IMG-OFFSET1


| Triangle  | Leg a (cm) | Leg b (cm) | Hypotenuse c (cm) | Angle α (°) | Angle β (°) | Right Angle (°) |
|---|---|---|---|---|---|---|
| T1 | 288.00 | 41.50 | 291.00 | 8.21 | 81.79 | 90.00 |
| T2 | 289.00 | 47.00 | 292.80 | 9.24 | 80.76 | 90.00 |
| T3 | 286.00 | 58.00 | 291.82 | 11.46 | 78.54 | 90.00 |
| T4 | 263.00 | 112.00 | 286.00 | 22.94 | 67.06 | 90.00 |
| T5 | 251.00 | 132.00 | 283.10 | 27.74 | 62.26 | 90.00 |
| T6 | 267.00 | 92.00 | 282.37 | 19.03 | 70.97 | 90.00 |
| T7 | 279.00 | 55.00 | 284.37 | 11.14 | 78.86 | 90.00 |
| T8 | 279.00 | 63.00 | 286.02 | 12.73 | 77.27 | 90.00 |
| T9 | 279.00 | 65.00 | 286.47 | 13.12 | 76.88 | 90.00 |
| T10 | 278.00 | 74.00 | 287.68 | 14.91 | 75.09 | 90.00 |
| Average | 275.90 | 73.95 | 287.16 | 14.15 | 75.85 | 90.00 |

Therefore, we had to modify the dimensions of our steering knuckles, as they had a fairly high level of backlash, which was causing those results in the robot. Once the knuckle measurements were changed, we achieved a deviation of 4.88° ± a standard deviation of 2.61 degrees.

You can see here the STL archive of the Steering Kuckels whit the new adjustments: [Steering Knuckles Rev2](/models/Open_Championship_Panama/S25_Mangueta_Rev2.STL)

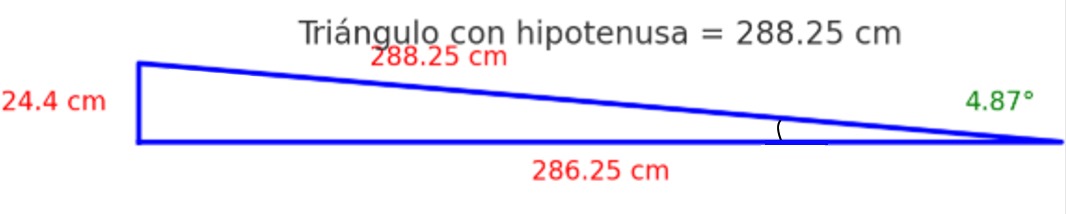
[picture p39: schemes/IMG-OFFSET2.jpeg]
IMG-OFFSET2


| Triangle  | Leg a (cm) | Leg b (cm) | Hypotenuse c (cm) | Angle α (°) | Angle β (°) | Right Angle (°) |
|---|---|---|---|---|---|---|
| T1 | 279.00 | 26.00 | 280.21 | 5.32 | 84.68 | 90.00 |
| T2 | 289.00 | 36.00 | 291.23 | 7.10 | 82.90 | 90.00 |
| T3 | 276.00 | 48.00 | 280.14 | 9.86 | 80.14 | 90.00 |
| T4 | 291.00 | 19.00 | 291.62 | 3.74 | 86.26 | 90.00 |
| T5 | 290.00 | 15.00 | 290.39 | 2.96 | 87.04 | 90.00 |
| T6 | 290.00 | 22.00 | 290.83 | 4.34 | 85.66 | 90.00 |
| T7 | 286.50 | 35.50 | 288.69 | 7.06 | 82.94 | 90.00 |
| T8 | 288.00 | 11.50 | 288.23 | 2.29 | 87.71 | 90.00 |
| T9 | 288.00 | 5.00 | 288.04 | 1.00 | 89.00 | 90.00 |
| T10 | 291.00 | 26.00 | 292.16 | 5.11 | 84.89 | 90.00 |

These changes were carried out because no matter how good our gyro-based PD control was, there was an underlying mechanical problem. It is well known that hardware issues cannot be solved with software.

Similarly, we use the gyro sensor for the robot's turns. Upon reaching the desired point, the robot turns the wheels and moves forward until it detects the target angle. Once reached, it stops the motors and returns the steering to the neutral position.

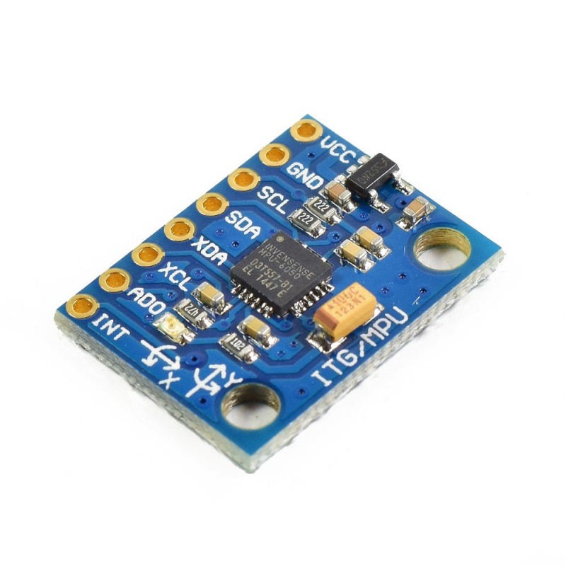
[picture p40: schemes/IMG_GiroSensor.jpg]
IMG_GiroSensor


**Update 12/09/2025: Inertial Measurement Unit (IMU) Replacement**

**Reason:** The previous IMU (GY-521) exhibited intermittent reading failures, characterized by a lock-up or saturation of its output values. This behavior caused inaccuracies in determining the vehicle's orientation, affecting the reliability of our test runs.

**Action:** The unit was replaced with a **GY-9250** model (which integrates the MPU-9250 and BMP280 sensors), selected for its reported higher stability and reliability.

**Replication Note:** For the purpose of replicating the base system, the previous sensor model is functional. This update addresses a specific need for robustness and precision during continuous operation.

IMG-GY9250

Power and Sensor Management
====

## Energy
The robot uses **six 3.7V 9900mAh (18650) batteries**. They are divided into **four battery holders connected in parallel** to manage current efficiently. The system's maximum voltage is **8.4V**.

To power our **Raspberry Pi 4 computer**, we use an **LM2596 voltage regulator set to 5.1V**. This allows the board to function correctly without needing to be plugged into a wall outlet. It's important to note that we initially conducted tests for obstacle management with the Pi connected to a wall outlet, which allowed us to validate our code's behavior. However, it was evident that we needed to solve this power issue for the robot to be fully autonomous.

IMG_Baterias_3.7v

## Ultrasonic Sensors
At the start of the season, our initial proposal was to use **VL53L0X laser sensors**. We thought they would be the best option due to their long range and precision, so our first chassis was designed for them. During testing, we realized their characteristics were problematic for us: the **conical field of view** caused the sensors to detect the floor, leading to many failures. Furthermore, using 3 of these sensors consumed an excessive amount of our microcontroller's memory (at that time, an Arduino UNO).

In our specific case, the decision to discard the laser sensors was primarily because we did not consider the points mentioned earlier. If at any point someone wishes to replicate this project, please note that with the necessary modifications, these sensors could be used and potentially yield better results than ours. As a recommendation, we can say that if others wish to use them, they should have a microcontroller with greater memory capacity, and the sensors should be positioned at least 5 cm above the ground.

IMG_SensorLaser

These issues led us to replace them with **HC-SR04 ultrasonic sensors**. We used these in the regional competition, and they remain in our current model. The change was straightforward thanks to our modular design; the mounts for the ultrasonic sensors we had designed for previous projects used the same mounting system as the laser sensor mounts on the chassis, making the transition quick and easy.

We have **3 ultrasonic sensors:** 1 at the front and 2 on the sides. The side sensors are primarily used to determine the turning direction. Once the robot leaves the first quadrant, there will always be one side with a barrier and one without. The sensor detecting the greater distance will dictate the turn direction (clockwise or counterclockwise).

The front sensor has multiple functions:

1. In the "Free Turn" challenge, it detects the distance to the wall before turning. Upon detecting 50 cm, the robot stops and proceeds to turn.

2. In the "Obstacles" challenge, it detects proximity to an obstacle. Upon detecting less than 15 cm, it stops and turns in the direction indicated by the color.

IMG_SU

## HMI (Human-Machine Interface)
On the vehicle's third level, there is a mini protoboard (170 points) with **3 LEDs and a button**. A passive buzzer is also mounted on the chassis.

**Free Turn Challenge:** When the start button is pressed, an LED turns on and the buzzer plays a sound, indicating that the code is running.

**Obstacles Challenge:** Depending on the case detected by the camera, different LEDs light up to provide visual feedback, and the buzzer plays distinct sounds for each case.

**Note:** The buzzer also generates a sound whenever the ultrasonic sensors detect an object.

Obstacle Management
===
## Camera
For the obstacle challenge, we chose to use a **Raspberry Pi Camera rev.1.3.** This section only details how we mounted the camera on the vehicle and the models used. For information on the detection algorithm and the obstacle avoidance solution, please refer to the [src](/src) folder.

Before using the official Raspberry camera, we used the ***Night Vision Camera for Raspberry Pi - IR-CUT 5MP model.** As the name implies, it is a night vision camera. When testing it with OpenCV, the image had a red filter that prevented our color detection algorithm from working correctly. The color values varied drastically depending on the environment, requiring very specific lighting conditions, which was a major problem.

IMG_Camera_VN

The solution was to switch to the standard Raspberry Pi camera. This change immediately resolved the issue, allowing the robot to function reliably in different environments. With this resolved, we proceeded to design and implement a custom mount for the camera, taking ideas from various designs for our solution.

IMG_Camera_RB1.3

## Position Control

*You are about to see all the information contained in our [src](/src/README.md). folder. If you wish to only view the information from this specific section, you can access it directly via the hyperlink (with the exception of the updates for the Panama Open Championship).*

**Encoder**

To determine how much the robot has moved, we use the encoder incorporated into our motor. Specifically, it is a HALL encoder: a device that uses **Hall** effect sensors to detect rotational movement and convert it into an electrical signal indicating position or speed.

**What is the** ***Hall effect?*** The Hall effect is the appearance of a potential difference (or electric field) transverse to an electrical conductor when an electric current flows through it and, simultaneously, a magnetic field is applied perpendicular to the direction of the current.

We implemented PID control software to make the robot advance the specific number of pulses we command. With the PID control, we ensure the robot does not fall significantly short of or exceed the target pulse count, thus achieving greater consistency in our vehicle's test runs. So far, we have managed to maintain the error within a range of ±4 pulses. This software is incorporated into both the Free Turn and the Obstacles challenges.

- [CTRL_POS](/src/CTRL_POS.ino).

**Gyro Sensor**

The use of this sensor is fundamental for our vehicle's operation. It has only two objectives, but they are very important:

1. Moving in a straight line **(Both challenges)**.
2. Make Turns.

**1. Straight-Line Movement:** To ensure the robot follows a trajectory without significant deviation, we use a PD control system to maintain the robot at the 0° angle of the gyroscope's Z-axis. We use a GY9250 Accelerometer/Gyroscope. To maintain the same angle, the control system adjusts the steering using the servo motor. This means that if the robot deviates, the steering system turns in the opposite direction to the deviation, allowing the robot to stay centered. As expected, it doesn't always stay perfectly parallel to the trajectory; over very long distances, there is a deviation of no more than 2 degrees, but it remains within our specified tolerances.

**2. Making Turns:** All turns the robot makes on the track are based on the gyro sensor. It's important to clarify that for making turns, the robot's steering moves to the maximum possible position (Left or Right). We do not adjust the steering to intermediate positions for turns, as this would introduce many more variables to consider. Once the steering is in position for the turn, the vehicle moves forward until it reaches the target angle indicated by the gyro sensor. When it stops, the steering returns to the center position, and the robot continues with its routine.

## Ultrasonic Sensors

**Front Sensor**

As mentioned in other sections of the repository, our robot is equipped with 3 ultrasonic sensors: one on the front and two on the sides (one per side). The front sensor has two main functions:

  1. To detect the distance between the robot and the track barriers **(Open Challenge).**
  2. To obtain the distance between the robot and the obstacles **(Obstacle Challenge).**

1. Open & Obstacle Challenge Barrier Detection: In both the Free Turn and Obstacles challenges, the robot uses the front ultrasonic sensor to detect when it is close to the barrier in front of it. When the distance reaches ≤ 64 cm, the vehicle stops and turns in the direction indicated by the side sensors. This allows us to maintain greater consistency when executing turns in both challenges.
   
2. Obstacle Challenge Proximity Sensing: In the Obstacle challenge, when the robot positions itself in front of an obstacle, the sensor detects the distance between the obstacle and the vehicle. This allows the robot to know its proximity to the obstacle and determine how wide or tight the turn needs to be.

he code for using the ultrasonic sensors is located in the [funciones](/src/S25_Obstaculos_29_08_2025/Funciones.ino) file. This file contains most of the functions we use in our main code.

**Side Sensors**

The side sensors serve several objectives in our vehicle, which are as follows:

1. Determine the direction of rotation (Clockwise/Counter-clockwise).
2. Wall following.
3. Detect the inner barriers.
4. Detect the parking boundaries.

Previously, the sensors shared the same port for the **Trigger** pin using a Y-cable. Initially, we did this because our microcontroller was an Arduino UNO, which saved ports, and we thought it was a good idea as it also simplified the code. However, due to our vehicle's needs and the additional sensors we integrated over time, the Arduino UNO had insufficient ports, forcing us to upgrade to an Arduino MEGA. Despite this change, we continued with the shared trigger configuration for the side sensors. Over time, we noticed the sensors exhibited erratic behavior or did not always return accurate distances. For this reason, leveraging the abundance of digital ports on the new microcontroller, we modified the setup so that each sensor now has its own dedicated trigger port.

The objectives of the side sensors are explained below:

1. **Turn Direction:** In both challenges, when the robot makes its first turn to head to another quadrant, we call the *twoSUS* function to get the distance detected by both sensors. Depending on which sensor detected the greater distance, we determine the turn direction for the run: if the right sensor had the greater distance, the direction is clockwise; if the left sensor had the greater distance, it is counter-clockwise.
   
2. **Wall Following:** In the Obstacle challenge, we use a PD follower to track the outer barriers in cases where there are one or two green objects in the quadrant (the development of the obstacle avoidance algorithm will be discussed later). After completing the quadrant with obstacles, the robot positions itself to detect the obstacles in the next obstacle quadrant.

3. **Inner Barrier Detection:** In cases involving at least one red object, the robot uses the side sensor facing the inner barriers to align with them. This provides greater control over the robot's position after avoiding the red obstacle. We previously also used wall following for scenarios involving red objects, but since the distance traveled was very short, the robot would end the following routine in inconsistent positions, making it very difficult to position itself for the next quadrant or obstacle.

4. **Parking Boundary Detection:** The name of this objective is self-explanatory. When the robot completes the three laps, we use one of the side sensors (depending on the turn direction) to detect one of the parking boundaries to initiate the parking routine.

## Obstacle Management 

**Algorithm**

The category rules mention 36 possible obstacle position cases. To solve this challenge, our team first discussed the best approach, as it's crucial to correctly define the problem before programming. After several hours of discussion, we arrived at the following solution: the position cases can be simplified to just 4 core scenarios:

- Red
- Green
- Green - Red
- Red - Green

Regardless of their specific location within the quadrant, all cases reduce to these 4 configurations. Therefore, our solution was to program routines for these 4 cases. After avoiding the obstacles in one quadrant, the robot positions itself to detect the obstacles in the next quadrant. This process repeats in a loop until the 3 laps are completed.

**Object and Color Detection Program**

Our camera program divides the screen's view into zones and highlights the contour of the obstacles, ignoring contours smaller than the area covered by the actual obstacles. It changes the value of a variable depending on the color of the obstacle detected in front of it and selects the case based on the color and position of the objects. To determine the position of the obstacles, we use the camera's pixels on the Y-axis; the case is determined by the pixel location and the color of the object's contour.

Since the robot uses both a Raspberry Pi and an Arduino, the camera sends these values to the Arduino via the serial port by printing the value and transmitting it. The Arduino then performs an action based on the received value. To provide a simpler visual confirmation of the detected case, the robot has 4 LEDs, and one lights up for each specific case detected. As an additional feedback mechanism, it also generates different sound frequencies depending on the case.

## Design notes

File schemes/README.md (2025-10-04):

Electrical Diagrams
====

This section presents the electrical diagrams of all components along with a description of their operation. Furthermore, it breaks down the robot's hardware and its integration with the mechanical parts. All 3D models and designs mentioned here are available in the [models](/models) folder.

## General Vehicle Electrical Diagram: 

DE-S25_bb

***Specifications:*** The **Arduino MEGA** board is powered directly through the serial communication port of the **Raspberry Pi 4** computer. The Raspberry Pi, in turn, is powered by our **LM2596** voltage regulator, set to **5.1V** and **3A**. We adjusted the regulator to 5.1V because when set exactly to 5V, the Raspberry Pi would often experience power supply issues.

## Electrical Diagrams for Each Component and Sensor:

***Clarification:*** The following diagrams show the signal connections for each sensor and electrical component. **Only* the **Power System** and **Motor with Motor Driver** diagrams include the power supply connections, as these are essential for replicating the robot. The other diagrams omit these connections to provide flexibility for other teams, but they can be referenced in the **General Electrical Diagram** shown above.

- **Ultrasonic Sensors**
  
IMG-DE_SUS

- **Accelerometer/Gyroscope**
  
IMG-DE_Gyro

- **Servo Motor**
  
IMG-DE_Servo

- **Human Machine Interface**
  
IMG-DE_HMI

- **Motor 12v - Motor Driver**
  
IMG-DE_Motor_MDirver

- **Power Stage and Raspberry Pi 4**
  
IMG-DE_Potencia

Mobility Management
===
## 12V DC Motor with Encoder
We selected this motor primarily for its **integrated encoder**. This sensor allows us to track the robot's position, which provides multiple benefits for our solution: calculating rotation count, measuring distance traveled, assisting in parallel parking, and, in general, all variables related to positioning.

IMG-Motor12v

Initially, we used a motor from an RC toy that included a differential. We used that motor during the regional stage in Mexicali. We decided to change it because its speed was too inconsistent, and the lack of an encoder made it very difficult to maintain consistent movements. We understand that it's impossible for a robot to repeat a routine exactly, but that component made it even more challenging. Switching to a motor with an encoder and a LEGO differential gives us much greater control over these variables. To achieve this, we designed a mount to couple the motor to the LEGO differential, which went through 3 revisions.

IMG_Soporte_Motor_Rev1

*This is what the first version looked like. It allowed for basic testing, but the motor was not secured to the mount, which caused disturbances and instability.*

-[Soporte para motor Rev3](/models/S25_Soporte_Motor_y_Transmision_Rev3.STL) 

*In the current revision, the motor is firmly secured to the mount, eliminating disturbances caused by movement.* We had a similar case with the gear that connects to the motor.

## Movement 
To make the robot move in a straight line, we use a gyro sensor with a PD controller. This allows the robot to maintain its heading. As mentioned before, it's impossible to be perfect, but with this system the deviation is minimal, never exceeding 2° from the initial point (considering 0° as the origin).

IMG_Offset

Similarly, we use the gyro sensor for the robot's turns. Upon reaching the desired point, the robot turns the wheels and moves forward until it detects the target angle. Once reached, it stops the motors and returns the steering to the neutral position.

IMG_GiroSensor

**Update 12/09/2025: Inertial Measurement Unit (IMU) Replacement**

**Reason:** The previous IMU (GY-521) exhibited intermittent reading failures, characterized by a lock-up or saturation of its output values. This behavior caused inaccuracies in determining the vehicle's orientation, affecting the reliability of our test runs.

**Action:** The unit was replaced with a **GY-9250** model (which integrates the MPU-9250 and BMP280 sensors), selected for its reported higher stability and reliability.

**Replication Note:** For the purpose of replicating the base system, the previous sensor model is functional. This update addresses a specific need for robustness and precision during continuous operation.

IMG-GY9250

Power and Sensor Management
====

## Energy
The robot uses **six 3.7V 9900mAh (18650) batteries**. They are divided into **four battery holders connected in parallel** to manage current efficiently. The system's maximum voltage is **8.4V**.

To power our **Raspberry Pi 4 computer**, we use an **LM2596 voltage regulator set to 5.1V**. This allows the board to function correctly without needing to be plugged into a wall outlet. It's important to note that we initially conducted tests for obstacle management with the Pi connected to a wall outlet, which allowed us to validate our code's behavior. However, it was evident that we needed to solve this power issue for the robot to be fully autonomous.

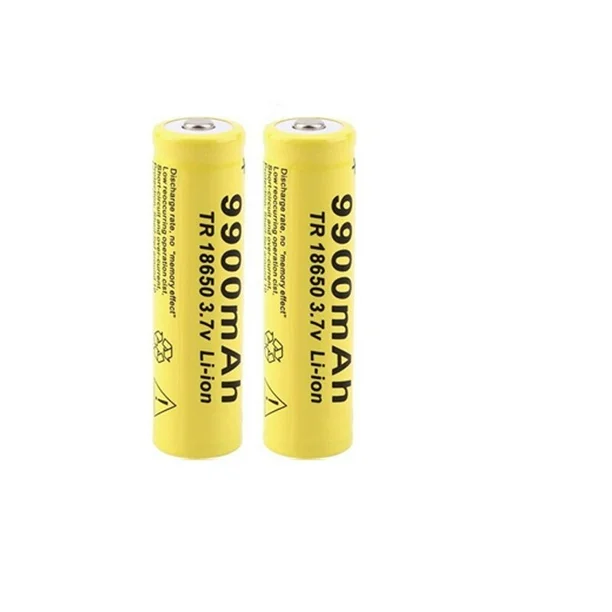
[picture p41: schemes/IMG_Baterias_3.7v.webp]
IMG_Baterias_3.7v


## Sensors
At the start of the season, our initial proposal was to use **VL53L0X laser sensors**. We thought they would be the best option due to their long range and precision, so our first chassis was designed for them. During testing, we realized their characteristics were problematic for us: the **conical field of view** caused the sensors to detect the floor, leading to many failures. Furthermore, using 3 of these sensors consumed an excessive amount of our microcontroller's memory (at that time, an Arduino UNO).

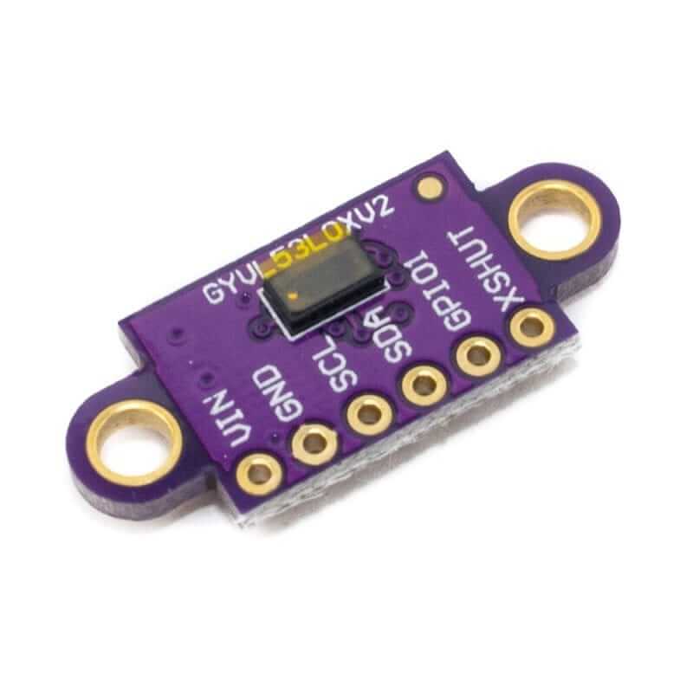
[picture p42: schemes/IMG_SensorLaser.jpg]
IMG_SensorLaser


These issues led us to replace them with **HC-SR04 ultrasonic sensors**. We used these in the regional competition, and they remain in our current model. The change was straightforward thanks to our modular design; the mounts for the ultrasonic sensors we had designed for previous projects used the same mounting system as the laser sensor mounts on the chassis, making the transition quick and easy.

We have **3 ultrasonic sensors:** 1 at the front and 2 on the sides. The side sensors are primarily used to determine the turning direction. Once the robot leaves the first quadrant, there will always be one side with a barrier and one without. The sensor detecting the greater distance will dictate the turn direction (clockwise or counterclockwise).

The front sensor has multiple functions:

1. In the "Free Turn" challenge, it detects the distance to the wall before turning. Upon detecting 50 cm, the robot stops and proceeds to turn.

2. In the "Obstacles" challenge, it detects proximity to an obstacle. Upon detecting less than 15 cm, it stops and turns in the direction indicated by the color.

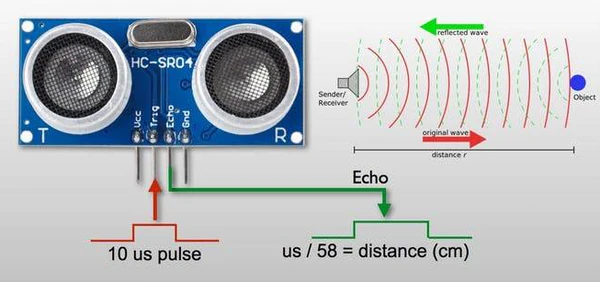
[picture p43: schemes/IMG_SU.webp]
IMG_SU


## HMI (Human-Machine Interface)
On the vehicle's third level, there is a mini protoboard (170 points) with **3 LEDs and a button**. A passive buzzer is also mounted on the chassis.

**Free Turn Challenge:** When the start button is pressed, an LED turns on and the buzzer plays a sound, indicating that the code is running.

**Obstacles Challenge:** Depending on the case detected by the camera, different LEDs light up to provide visual feedback, and the buzzer plays distinct sounds for each case.

**Note:** The buzzer also generates a sound whenever the ultrasonic sensors detect an object.

Obstacle Management
===
## Camera
For the obstacle challenge, we chose to use a **Raspberry Pi Camera rev.1.3.** This section only details how we mounted the camera on the vehicle and the models used. For information on the detection algorithm and the obstacle avoidance solution, please refer to the [src](/src) folder.

Before using the official Raspberry camera, we used the ***Night Vision Camera for Raspberry Pi - IR-CUT 5MP model.** As the name implies, it is a night vision camera. When testing it with OpenCV, the image had a red filter that prevented our color detection algorithm from working correctly. The color values varied drastically depending on the environment, requiring very specific lighting conditions, which was a major problem.

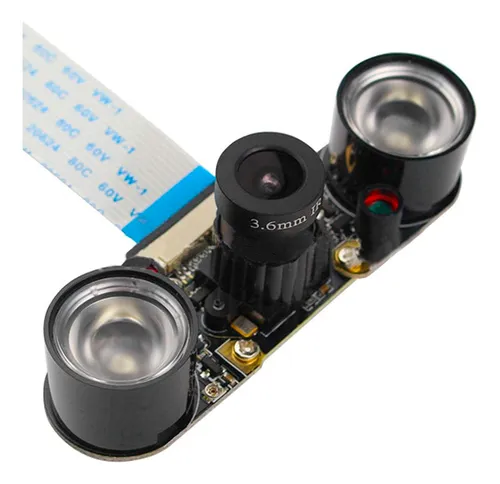
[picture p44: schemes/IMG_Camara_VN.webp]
IMG_Camera_VN


The solution was to switch to the standard Raspberry Pi camera. This change immediately resolved the issue, allowing the robot to function reliably in different environments. With this resolved, we proceeded to design and implement a custom mount for the camera, taking ideas from various designs for our solution.

IMG_Camera_RB1.3

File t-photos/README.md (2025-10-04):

Team's photos
====

You can find the team photos in this section.

- **Formal Photo**
  
The photo shows the 3 team members (from left to right):

Jacobo Arteaga Castañeda - Diego Alejandro Salas Díaz - Andrea Perez Bueno (Coach)

IMG-Serius

- **Funny Photo**
  
The photo captures the "birth" of our robot :)

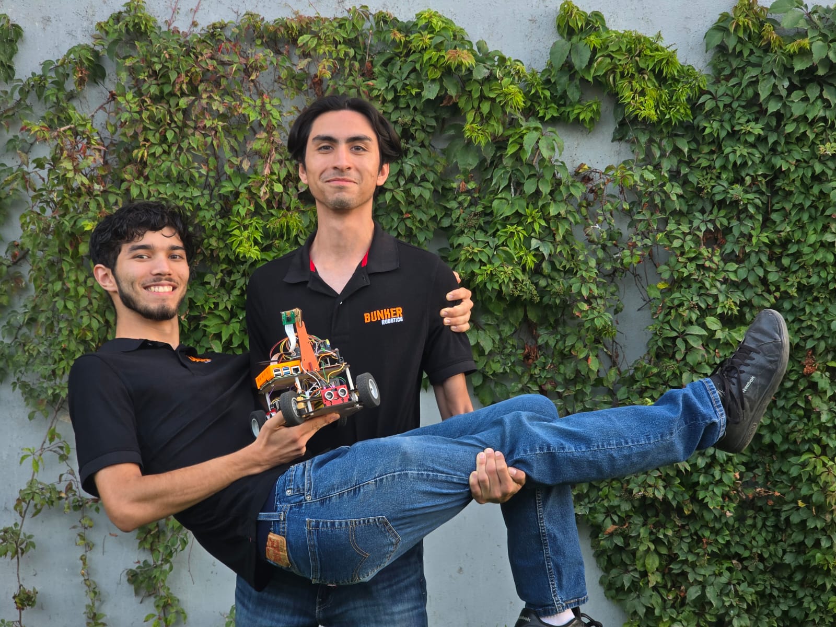
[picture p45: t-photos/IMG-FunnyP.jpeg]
IMG-FunnyP


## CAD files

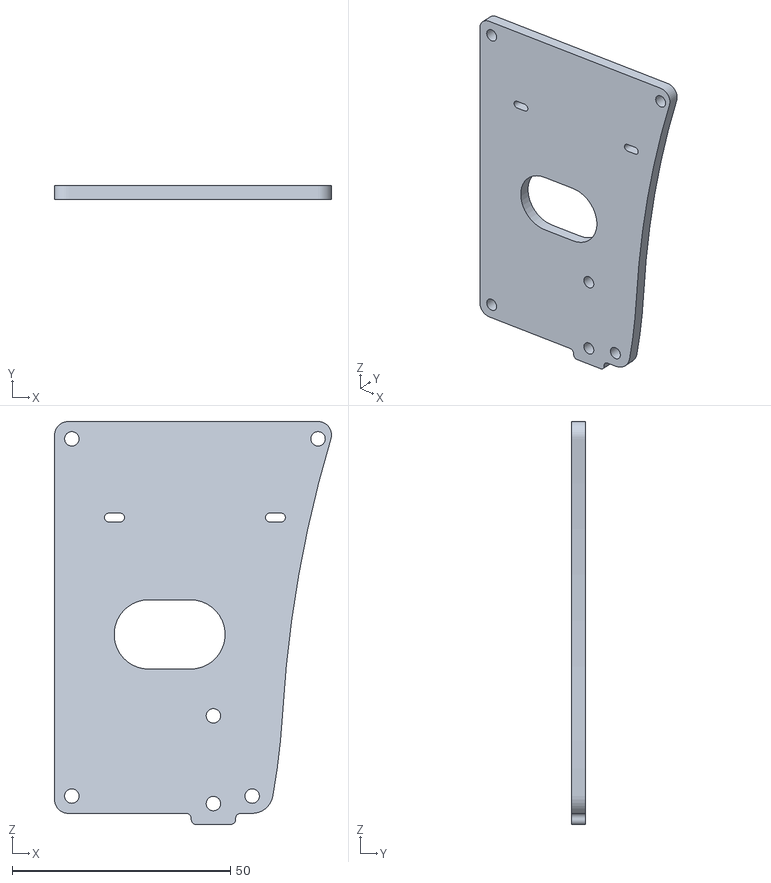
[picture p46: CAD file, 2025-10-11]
models/Open_Championship_Panama/S25_3er_Piso_Rev3.STL
63.4 x 3.12 x 92.2

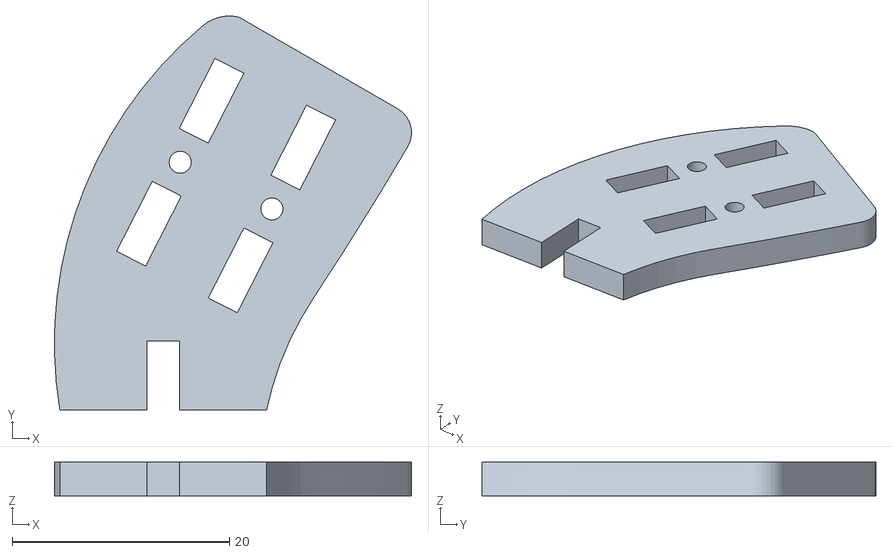
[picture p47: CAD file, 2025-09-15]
models/S25_Union63_grados_Poste-Soporte_CamaraRev2.STL
32.9 x 36.3 x 3.12

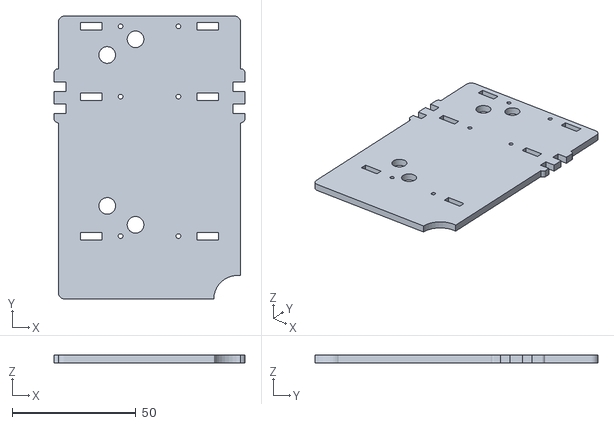
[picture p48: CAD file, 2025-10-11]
models/Open_Championship_Panama/C3_Baterias_Rev3.STL
77.0 x 114.3 x 3.12

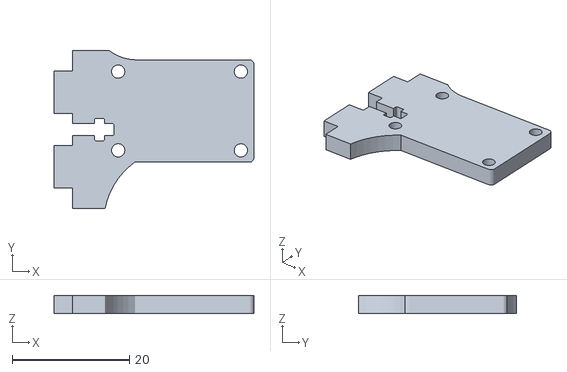
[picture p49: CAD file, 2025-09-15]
models/S25_Soporte_CamaraRev2.STL
34.1 x 27.0 x 3.12

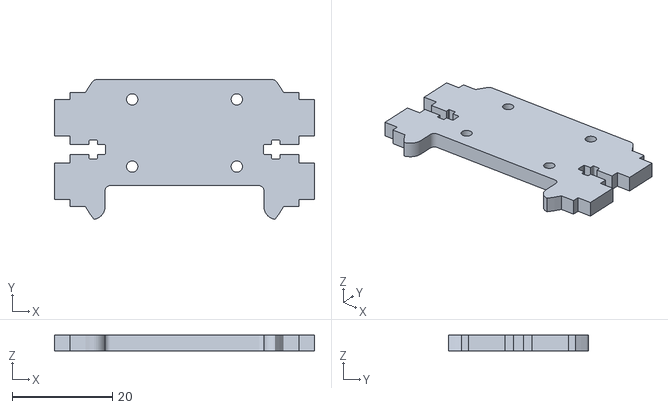
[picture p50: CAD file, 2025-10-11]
models/Open_Championship_Panama/Soporte_Camara_Rev3.STL
52.0 x 27.9 x 3.12

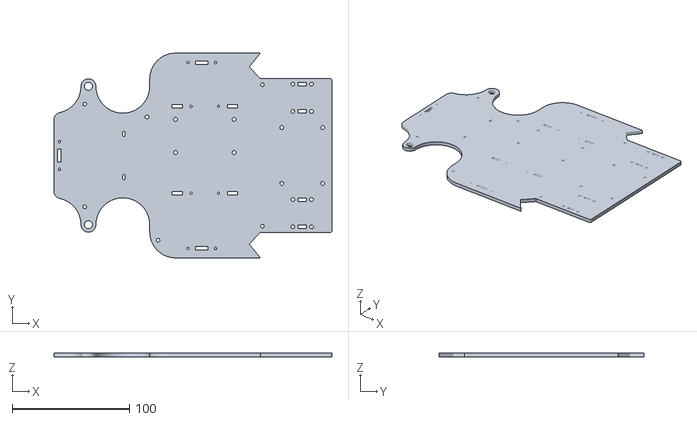
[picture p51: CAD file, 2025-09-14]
models/S25_Chasis_Rev14.STL
237.0 x 174.6 x 3.12

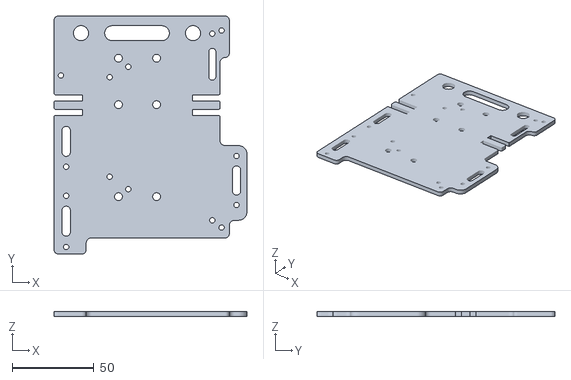
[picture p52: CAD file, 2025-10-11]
models/Open_Championship_Panama/BS_Baterias_Rev3.STL
118.1 x 145.7 x 3.12

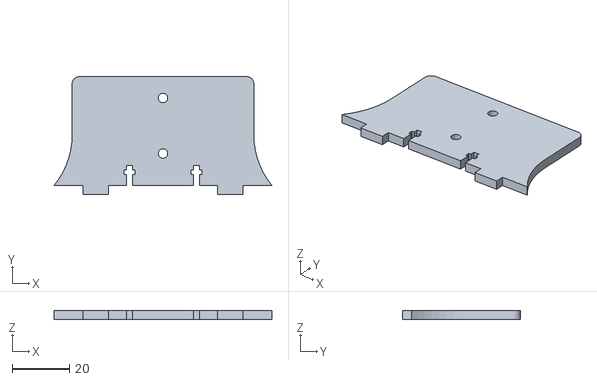
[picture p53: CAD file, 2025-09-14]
models/SB_DrakoR_Rev2.STL
76.2 x 41.2 x 3.12

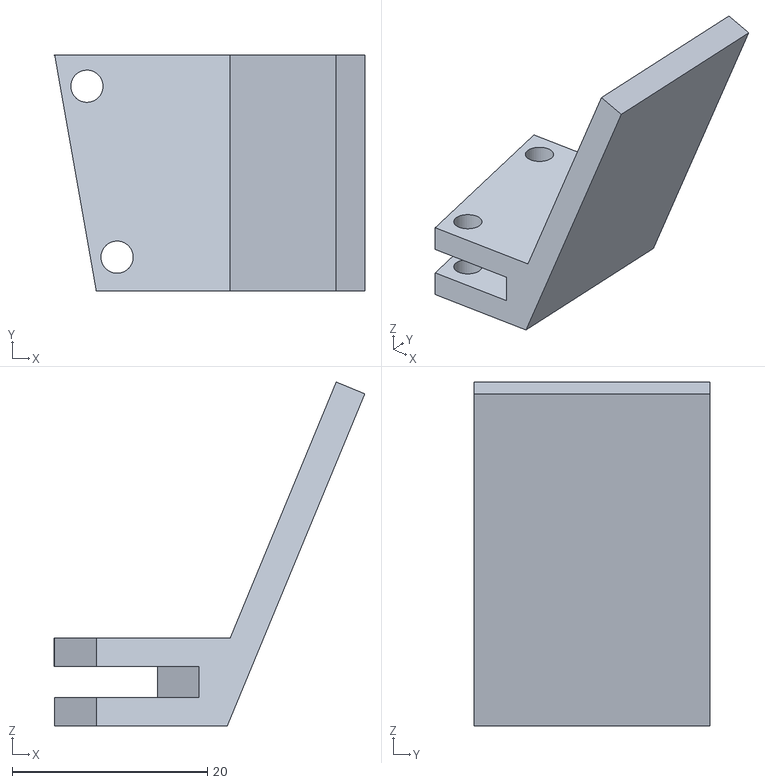
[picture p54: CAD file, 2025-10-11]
models/Open_Championship_Panama/Soporte_L_Rev1.STL
31.8 x 24.1 x 35.2

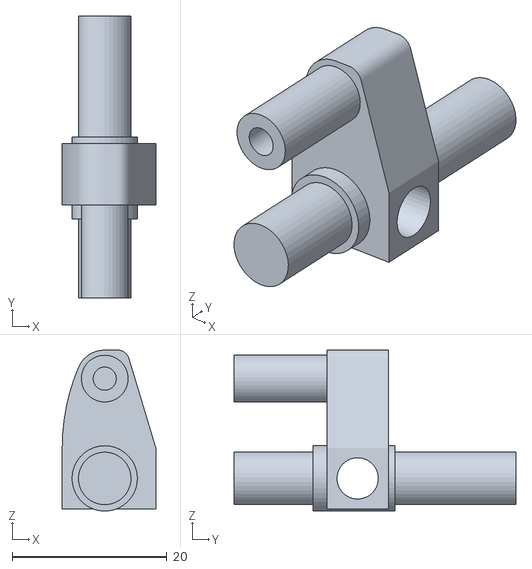
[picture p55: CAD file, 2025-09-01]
models/S25_Mangueta_Rev1.STL
12.1 x 36.4 x 20.8

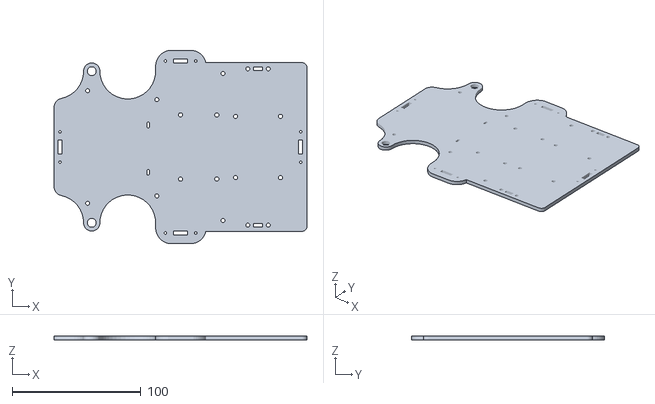
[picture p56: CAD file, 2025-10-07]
models/Open_Championship_Panama/S25_Chasis_Rev15B.STL
196.9 x 150.0 x 3.12

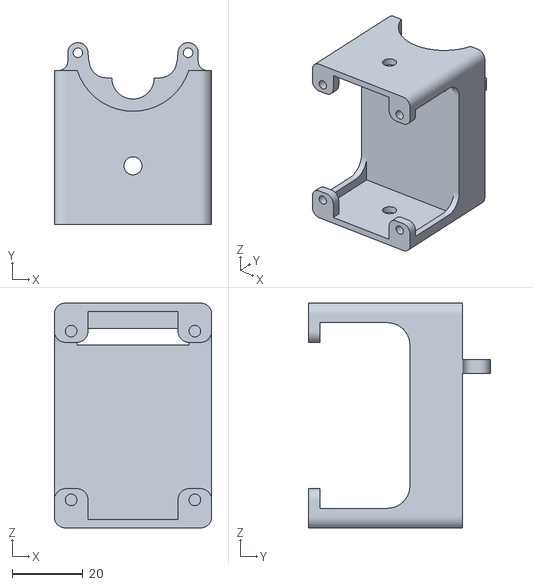
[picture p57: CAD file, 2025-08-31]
models/S25_Soporte_Motor_y_Transmision_Rev3.STL
44.5 x 51.3 x 63.5

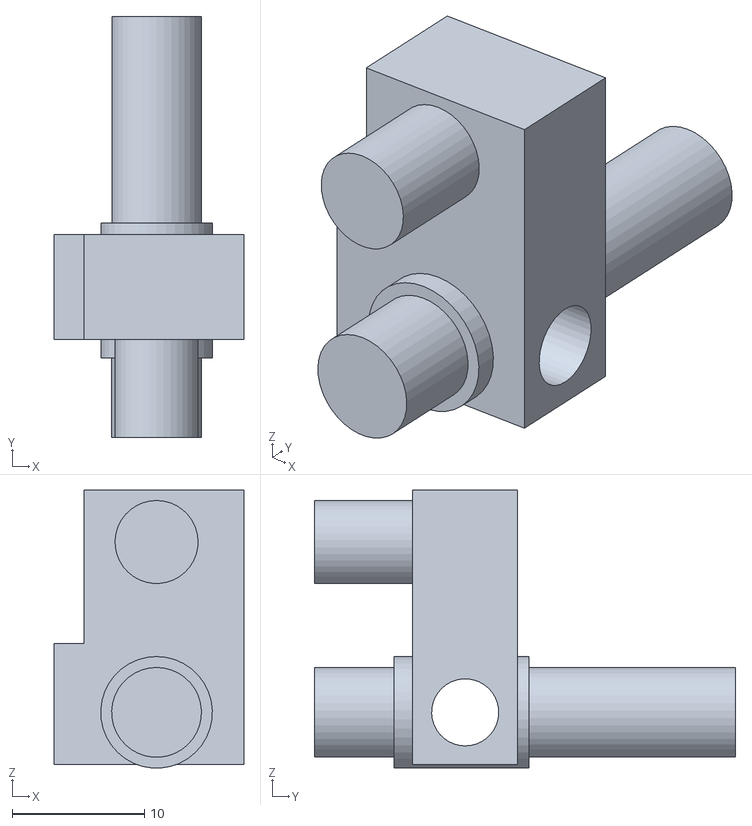
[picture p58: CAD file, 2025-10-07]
models/Open_Championship_Panama/S25_Mangueta_Rev2.STL
14.4 x 31.9 x 21.0

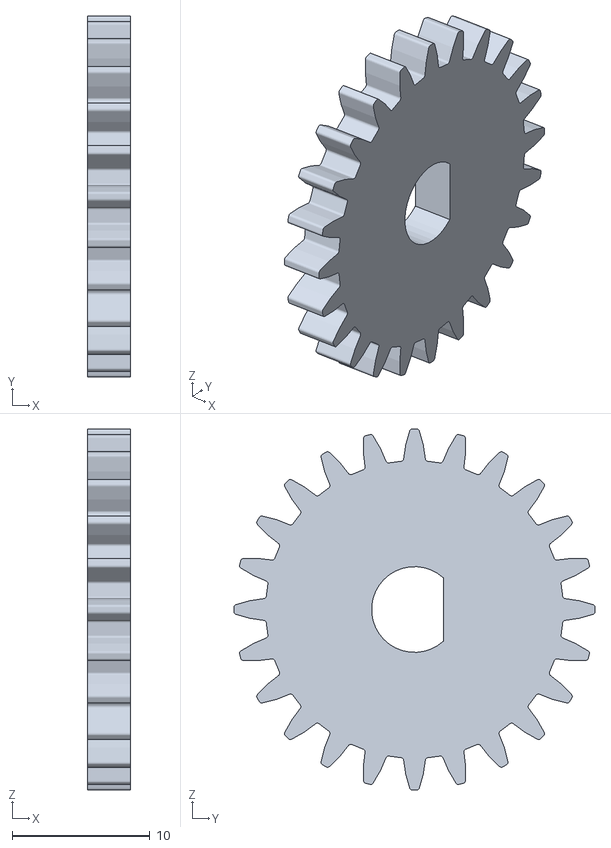
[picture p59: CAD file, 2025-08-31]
models/S25_Spur_24D_Rev3.STL
3.12 x 26.2 x 26.2

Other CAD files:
models/Open_Championship_Panama/S25_BS_Rev7.STL
models/S25_Soporte_Eje_Motor_Rev1.STL
models/S25_Union_70_grados_Camara_Rev1.STL
models/S25_Poste_Camara_Rev1.STL
models/S25_BS_Rev6.STL
models/S25_Chasis_Rev12.STL
models/S25_Conexion_Servo-enlace_Rev2.STL
models/S25_Enlace_Direccion_Rev5.STL
models/S25_Piso3_Rev1.STL
models/S25_Rondana_Direccion_Rev1.STL
models/S25_Soporte_Camara_Rev1.STL
models/S25_Soporte_Poste_Camara_Rev1.STL
models/S25_Soporte_Servo_Rev4.STL
models/S25_Spur_24D_Rev2.STL

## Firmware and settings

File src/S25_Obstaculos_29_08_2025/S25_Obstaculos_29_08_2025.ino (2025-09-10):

#include <Servo.h>
#include <Wire.h>
#include <MPU6050.h>

volatile int Contador = 0;

const int STBY = 8;

float pid, salida, h, tk, tk_1, error, u_error, I, D;
float Kp = 12, Ki = 0, Kd = 15;  // Kp = 12, Ki = 0, Kd = 15; 150  7.95v

// Motor A
const int PWMA = 12;
const int AIN1 = 10;
const int AIN2 = 11;

Servo SvD;
MPU6050 mpu;

///////////////////////////// Giro
//Angulos
float Gy = 0;
float Angle = 0;
int Grados = 0;

//MPU-6050 da los valores en enteros de 16 bits
//Valores RAW
int16_t GyX, GyY, GyZ = 0;

long tiempo_prev = 0;
float dt = 0;

//SUS
const int triggerPin1 = 31;
const int echoPin1 = 37;

const int echoPin2 = 35;

const int triggerPin3 = 4;
const int echoPin3 = 5;

float distance1 = 0;
float distance2 = 0;
float distance3;

#define PotVel A8
float VelRedu = 1;

int Cont = 0;
int ContAnterior = 0;
bool izq = false;

void dir(int Vi, int Vf, int T) {
  if (Vi < Vf) {
    for (int pos = Vi; pos <= Vf; pos += 1) {
      SvD.write(pos);
      delay(T);
    }
  } else {
    for (int pos = Vi; pos >= Vf; pos -= 1) {
      SvD.write(pos);
      delay(T);
    }
  }
}

void setup() {
  /*while (!Serial) {
    delay(1);
  }*/
  pinMode(3, INPUT_PULLUP);
  pinMode(triggerPin1, OUTPUT);
  pinMode(echoPin1, INPUT);
  pinMode(echoPin2, INPUT);
  pinMode(triggerPin3, OUTPUT);
  pinMode(echoPin3, INPUT);

  attachInterrupt(digitalPinToInterrupt(2), inter, RISING);
  // attachInterrupt(digitalPinToInterrupt(19), Gyro, CHANGE);

  pinMode(STBY, OUTPUT);

  pinMode(PWMA, OUTPUT);
  pinMode(AIN1, OUTPUT);
  pinMode(AIN2, OUTPUT);

  // Inicializamos motores apagados
  digitalWrite(STBY, LOW);

  SvD.attach(A1);  // Pin 1

  delay(50);

  mpu.initialize();

  // Verifica si la conexión fue exitosa
  if (mpu.testConnection()) {
    Serial.println("MPU-6050 conectado correctamente");
    tone(49, 244, 125);
    delay(625);
  } else {
    Serial.println("Error en la conexión del MPU-6050");
    tone(49, 800, 125);
    delay(625);
  }


  SvD.write(91.5);

  digitalWrite(40, 1);
  delay(200);
  digitalWrite(40, 0);
  delay(200);
  digitalWrite(41, 1);
  delay(200);
  digitalWrite(41, 0);

  delay(500);
  tone(49, 240, 125);
  digitalWrite(45, 1);

  while (digitalRead(23) == 0) {
    //Serial.print(".");
    delay(50);
  }
  //VelRedu = map(A8, 0, 1080, 0.3, 1);
  //Serial.println(VelRedu);
  tone(49, 587, 125);
  digitalWrite(45, 0);

  Serial.begin(9600);
  delay(125);

  inicio(90);
}

////////////////////////////////////////////////////////////////

void inicio(int dis) {
  Angle = 0;
  
  moverMotor(150);
  while (distance2 < dis && distance1 < dis) { twoSUS(40); }

  tone(49, 783, 125);
  SvD.write(91.5);

  distance3 = 100;
  moverMotor(120);
  while (distance3 >= 64) {
    SUS3();
    delay(10);
  }
  detenerMotores();

  tone(49, 110, 125);

  if (distance1 > 90) {
    izq = true;
  } else if (distance2 > 90) {
    izq = false;
  }

  digitalWrite(40, 1);
  delay(500);
  dir(91, 161, 8);
  delay(100);
  moverMotor(180);
  //Serial.println("Der");                      DERECHA
  while (Angle <= 87) { Gyro(1); }

  detenerMotores();
  tone(49, 3951, 125);
  delay(500);
  dir(161, 91, 8);

  delay(500);
}



//////////////////////////////////////////////////////////////////////////////////////////////////////////////////////////////////////////////////////////////////////////////////////////


void loop() {

  Serial.write('Z');

  deteccion('D');
  delay(10000000000000);
}


//////////////////////////////////////////////////////////////////////////////////////////////////////////////////////////////////////////////////////////////////////////////////////////




void deteccion(char caso) {

  delay(200);
  MotorEnc(-150, 245);
  detenerMotores();

  if (Serial.available() > 0 || caso != NULL) {

    char toSend = (char)Serial.read();
    if (toSend == 'N') {

    } else if (toSend == 'B' || caso == 'B') {  ////////////// Caso B VERDE VERDE
      detenerMotores();
      digitalWrite(41, 1);
      tone(49, 987, 125);
      delay(125);
      digitalWrite(41, 0);
      tone(49, 880, 125);
      delay(125);
      digitalWrite(41, 1);
      tone(49, 698, 125);
      delay(125);
      digitalWrite(41, 0);
      tone(49, 987, 125);
      delay(125);
      tone(49, 880, 125);

      EsqVerde1();

      MotorEnc(150, 1520);
      tone(49, 110, 125);

      inicio(111);

    }
    //////////////////////////////////////// Abajo

    else if (toSend == 'A' || caso == 'A') {  ////////////  Caso A  ROJO ROJO

      detenerMotores();
      digitalWrite(40, 1);
      tone(49, 698, 125);
      delay(125);
      digitalWrite(40, 0);
      tone(49, 880, 125);
      delay(125);
      digitalWrite(40, 1);
      tone(49, 987, 125);
      delay(125);
      digitalWrite(40, 0);
      tone(49, 698, 125);
      delay(125);
      tone(49, 880, 125);

      EsqRojo1();

      ContAnterior = Contador;
      delay(63);
      moverMotor(120);

      /////////////////////////////////////////////////
      PDPM(12, 0, 1, 900, 0, 12);
      SvD.write(91.5);
      Angle = 0;
      /////////////////////////////////////////////////

      detenerMotores();
      delay(200);

      moverMotor(120);
      while (distance2 < 90 && distance1 < 90) { twoSUS(40); }
      tone(49, 783, 125);
      MotorEnc(120, 320);
      tone(49, 110, 125);

      if (distance1 > 90) {
        izq = true;
      } else if (distance2 > 90) {
        izq = false;
      }
    }

    else if (toSend == 'C' || caso == 'C') {  ///////////// Caso C ROJO VERDE
      detenerMotores();
      digitalWrite(40, 1);
      tone(49, 987, 125);
      delay(125);
      tone(49, 880, 125);
      delay(125);
      digitalWrite(40, 0);
      tone(49, 698, 125);
      delay(125);
      digitalWrite(41, 1);
      tone(49, 880, 125);
      delay(125);
      digitalWrite(41, 0);
      tone(49, 987, 125);

      EsqRojoVerde1();
    }

    else if (toSend == 'D' || caso == 'D') {  ///////////// Caso D VERDE ROJO

      EsqVerdeRojo1();

      tone(49, 329, 125);
    }
  }
}


/*
  while (true) {}

  ///////////////////////////////////////
  SUS3();
  moverMotor(AIN1, AIN2, PWMA, 150);
  detenerMotores();
  tone(49, 3951, 125);
  delay(200);

  Angle = 0;
  dir(91, 49, 8);
  delay(125);
  moverMotor(AIN1, AIN2, PWMA, -130);
  while (Angle <= 45) { Gyro(1); }
  detenerMotores();
  tone(49, 110, 125);

  delay(125);
  dir(49, 91, 8);
  delay(125);
  Angle = 0;
  ContAnterior = Contador;
  moverMotor(AIN1, AIN2, PWMA, -130);
  while (Contador <= (ContAnterior + 320)) { Derecho(); }
  detenerMotores();

  delay(125);
  Angle = 0;
  dir(91, 49, 8);
  delay(125);
  moverMotor(AIN1, AIN2, PWMA, -130);
  while (Angle <= 45) { Gyro(1); }
  detenerMotores();
  tone(49, 110, 125);

  /////////////////////////////////////////
  while (true) {}

  delay(35);*/

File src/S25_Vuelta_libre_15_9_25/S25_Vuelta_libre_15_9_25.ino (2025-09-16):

#include <Servo.h>
#include <Wire.h>
#include <MPU6050_light.h>
MPU6050 mpu(Wire);

// Variables para el yaw
float yaw = 0.0;
unsigned long lastTime = 0;
float gyroZOffset = 0.0;

// Para calibración
bool calibrated = false;
const int CALIBRATION_SAMPLES = 500;

volatile int Contador = 0;

const int STBY = 8;

// Motor A
const int PWMA = 12;
const int AIN1 = 10;
const int AIN2 = 11;

Servo SvD;

//SUS
const int triggerPin1 = 31;
const int echoPin1 = 37;

const int echoPin2 = 35;

const int triggerPin3 = 53;
const int echoPin3 = 52;

float distance1 = 0;
float distance2 = 0;
float distance3 = 0;

int Cont = 0;
bool izq = false;

float global = 0;
int CV = 0;

void setup() {
  Wire.begin();
  Serial.begin(9600);
  pinMode(3, INPUT_PULLUP);
  pinMode(triggerPin1, OUTPUT);
  pinMode(echoPin1, INPUT);
  pinMode(echoPin2, INPUT);
  pinMode(triggerPin3, OUTPUT);
  pinMode(echoPin3, INPUT);

  Wire.beginTransmission(0x68);
  Wire.write(0x6B);
  Wire.write(0);
  Wire.endTransmission(true);

  attachInterrupt(digitalPinToInterrupt(3), inter, RISING);

  pinMode(STBY, OUTPUT);

  pinMode(PWMA, OUTPUT);
  pinMode(AIN1, OUTPUT);
  pinMode(AIN2, OUTPUT);

  // Inicializamos motores apagados
  digitalWrite(STBY, LOW);

  SvD.attach(A1);  // Pin 1
  delay(50);
  tone(49, 293, 125);
  delay(50);

  SvD.write(92);
  byte status = mpu.begin();
  Serial.print("MPU6050 status: ");
  Serial.println(status);
  while (status != 0) {}

  Serial.println("Calibrando, no mover el sensor...");
  mpu.calcOffsets();  // Calibración interna de la librería
  calibrateGyroZ();   // Calibración adicional específica para Z

  Serial.println("¡Calibración completada!");
  lastTime = millis();
  calibrated = true;

  tone(49, 1000, 125);

  twoSUS(40);
  if (distance1 != 0) {
    digitalWrite(40, 1);
    tone(49, 1760, 125);
    delay(200);
    digitalWrite(40, 0);
    delay(200);
  } else {
    tone(49, 4186, 125);
    delay(125);
    tone(49, 4186, 125);
    delay(125);
    while (true) {}
  }
  if (distance2 != 0) {
    digitalWrite(41, 1);
    tone(49, 1975, 125);
    delay(200);
    digitalWrite(41, 0);
    delay(200);
  } else {
    tone(49, 4186, 125);
    delay(125);
    tone(49, 4186, 125);
    delay(125);
    while (true) {}
  }

  delay(400);
  tone(49, 240, 125);
  digitalWrite(45, 1);

  while (digitalRead(23) == 0) {
    delay(50);
  }

  tone(49, 587, 125);
  digitalWrite(45, 0);

  delay(125);
  SvD.write(91);
  delay(400);
  distance3 = 53;
}

//////////////////////////////////////////////// Bucle principal
void loop() {  // 90 grados = 76.5 grados yaw
  SDLG();
  if (CV == 12) {
    MotorEnc(140,1275);
    delay(300);
    detenerMotores();
    delay(10000000000000000000000000000);
  }
}

////////////////////////////////////////// Función para saber a que lado girar
void SDLG() {
  SUS3();
  Serial.println(distance3);
  delay(10);
  if (distance3 <= 58) {
    detenerMotores();
    SvD.write(91);
    delay(225);
    CV++;
    if (CV == 4 || CV == 8 || CV == 12) {
      global = 0;
      yaw = 0;
    }
    twoSUS(20);
    if (distance2 > distance1) {
      Giros(1, 120);
      global = global + 71.5;
    } else {
      Giros(2, 120);
      global = global - 68.5;
    }
  } else {
    moverMotor(180);
    Derecho(2.96, 0, 0.35);
  }
}

void Estacionarse() {
  detenerMotores();
  tone(49, 3322, 375);
  delay(375);
  MotorEnc(-120, 300);
  moverMotor(120);

  if (izq == true) {
    while (distance1 > 90) {
      twoSUS(30);
      delay(30);
    }
  } else {
    while (distance2 > 90) {
      twoSUS(30);
      delay(30);
    }
  }
  detenerMotores();
  tone(49, 4186, 125);

  MotorEnc(150, 1200);

  tone(49, 2093, 125);
  detenerMotores();

  tone(49, 261, 125);
  delay(125);
  tone(49, 293, 125);
  delay(125);
  tone(49, 329, 375);
  delay(375);
  while (true) {}
}
